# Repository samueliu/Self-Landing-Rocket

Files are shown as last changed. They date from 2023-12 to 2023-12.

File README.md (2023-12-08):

# Self-Landing-Rocket
Democratization of Self-Landing Rocketry Capstone repository

Check out our Youtube Video!
https://m.youtube.com/watch?v=Z3JtFpSVZIc&feature=youtu.be 

# Project Description
The goal of this project is to provide research groups and hobbyists with an open source, sub-scale, self-stabilizing model rocket platform that will unlock previously inaccessible low-budget research/experimentation of 'inverted pendulum' self-landing rockets. This page contains details on the required materials and tools as well as build instructions.

Screenshot 2023-11-28 at 5 56 44 PM

# Fabrication Techniques and Materials
The following machines will be needed for fabrication
1. FDM Printer
2. Resin Printer
3. Desktop CNC Router
4. Soldering Iron
5. Drill
6. Dremel

Additionally, a full list of materials with links to purchasing sites can be found in the materials folder.
# Build/Assembly
There are three main components to this build. The first is machining, printing and cutting parts. The second is soldering the circuit schematic together and the third is epoxying and bolting together the full assembly. 

Step 1: Machining, Printing and Cutting

The parts to print are seperated into resin and FDM parts and can be found under the rocket hardware folder. The majority of the custom components on the vehcile are 3D printed primarily using FDM (Fused Deposition Modeling) but a select few parts were printed on SLA (Stereolithography) 3D printers. The rationale for using the SLA 3D printers primarily revolves around the need for increased component resolution/tolerance. For example, the two pitch and roll servo couplers mate to the T15 servo spline which has 15 teeth size on the order of a single millimeter. For accessability and ease of manufacture, the majority of the remainder of the custom components were printed on a FDM 3D printer as they are generally larger and require less fidelity. A lightweight thermoplastic filament called LW-PLA from PloyMaker was used with low infill (15%) to reduce the wieght of these larger FDM parts. 

A few number of select parts require CNC machining (including the four landing gear legs and the battery holder) as these parts have strict sitffness/mass requirements which could only be satisfied by fiberglass or carbon fiber. In order to meet the stiffness requirements that would be neccesary from supporting the thrust mechanism as well as shock from landing, 3mm Carbon fiber was chosen as the material for the landing gear legs. A desktop CNC router (Shapeoko 4) was used to cut the parts. The feed/punge rate was set to approximately 400mm/s and 150mm/s with a 1/16" 4 flute burr endmill and the CAD/CAM files can be found here under the rocket hardware folder.

A select number of components also required cutting/joining. The two carbon fiber shafts holding the motors were cut using a dremel and the rocket tube was cut using an X-acto knife. A part was also printed to help guide this X acto knife cut and can be found within the STL folder. Super glue was used to couple all 3D printed TVC parts to the respective carbon components except for joints experiencing large loads (carbon legs to rocket fuselage and carbon battery plate to nose cone) which were coupled using an off-the-shelf 5 minute epoxy.

Step 2: Circuit schematic



Above is the circuit schematic used in this project. A proto board was used for integrating all parts. 

Step 3: Putting it all Together

With all materials printed, machined and cut, as well as the electronics put together, the final step is to build the rocket. Provided are both an stl of the full build for easy reference, as well as an instructional manual with step by step build instructions. 

# Assembly details and CAD files

[Instruction Manual](Instruction_Manual.pdf)

[Final CAD Assembly Reference + Files](https://cad.onshape.com/documents/38c71b9123422c3013c80387/w/ad7e7c668ee5186588dc29fc/e/67ed507e38b5f468f95fb797)

[Project Summary & Analysis](Project_Summary_&_Analysis.pdf)

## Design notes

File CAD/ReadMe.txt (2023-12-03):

All of the CAD design for this poject was completed in the OnShape CAD design platform. Access to the OnShape project is by invite only given OnShape restrictions, so please email robbievanzyl@gmail.com to received access.

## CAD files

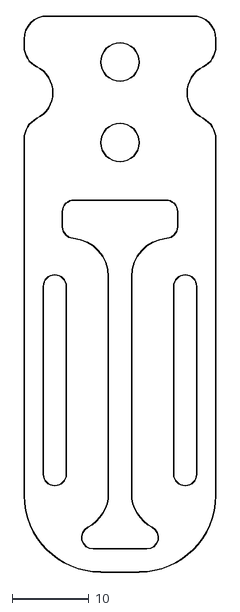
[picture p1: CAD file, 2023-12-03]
CAM/BatteryHolderPlate_CarbonFiber.dxf
25.0 x 72.5

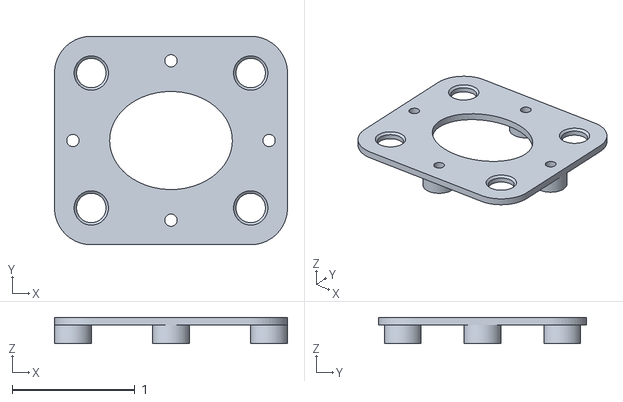
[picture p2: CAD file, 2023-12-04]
STL's/Fuselage and Body/IMU Mount Lower.stl
1.90 x 1.70 x 0.213

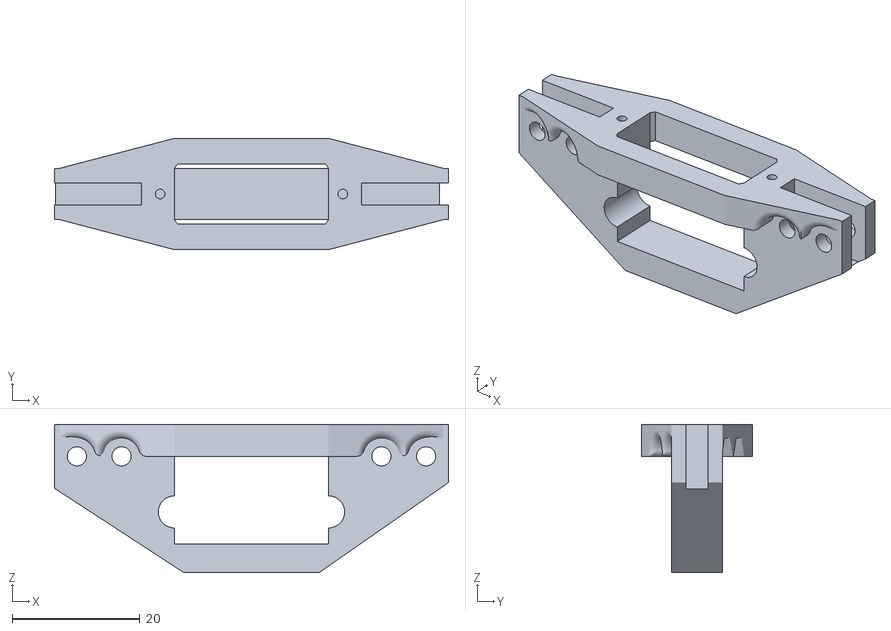
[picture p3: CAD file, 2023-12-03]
STL's/Thrust Vector Control (TVC) Mechanism/ServoLegMount_SLA.stl
61.7 x 17.4 x 23.2

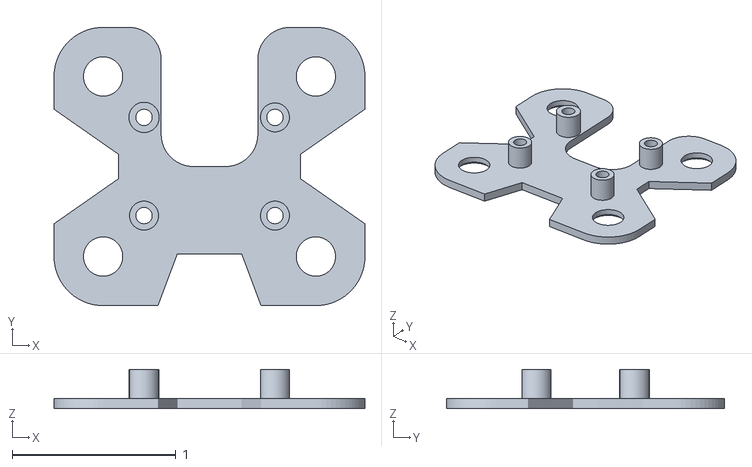
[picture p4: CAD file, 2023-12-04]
STL's/Fuselage and Body/IMU Mount Upper.stl
1.90 x 1.70 x 0.24

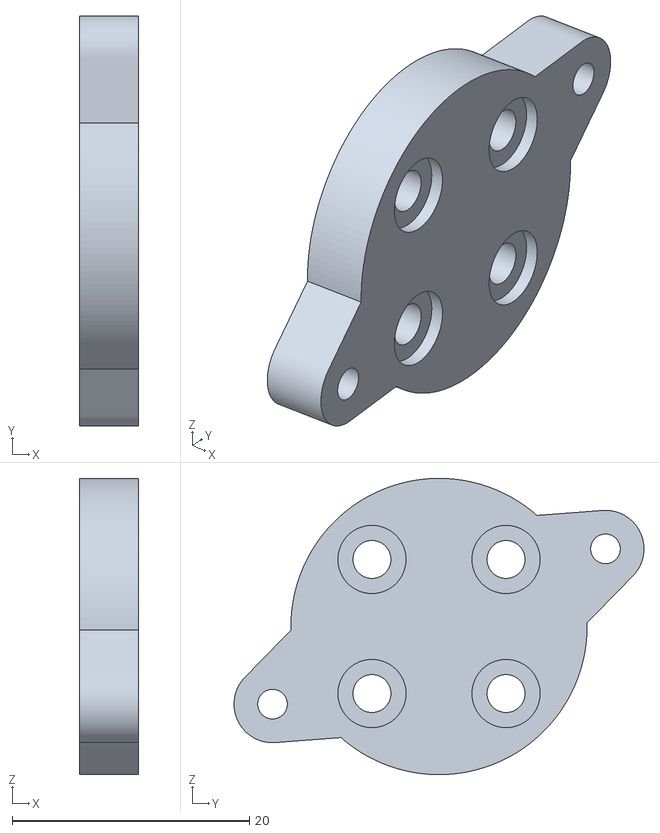
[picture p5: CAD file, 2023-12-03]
STL's/Thrust Vector Control (TVC) Mechanism/TopMotorPlate_SLA.stl
5.00 x 34.6 x 25.0

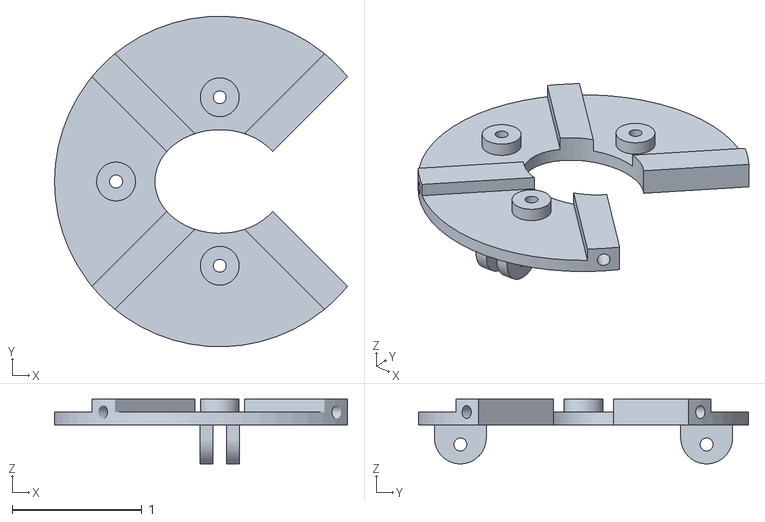
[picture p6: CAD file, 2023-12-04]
STL's/Fuselage and Body/Bottom Sensor Mount Holder.stl
2.26 x 2.55 x 0.5

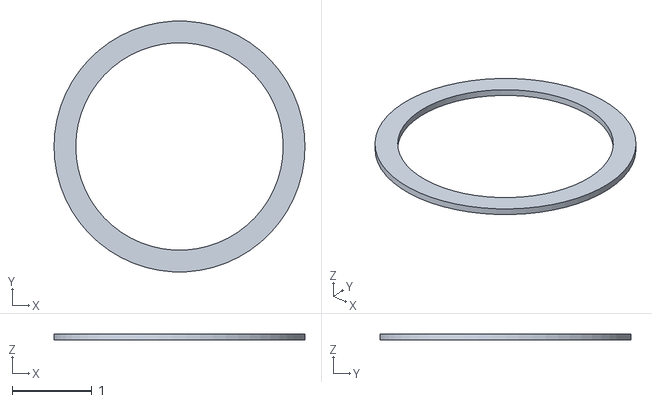
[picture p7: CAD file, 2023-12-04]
STL's/Fuselage and Body/Cutting Guide.stl
3.15 x 3.14 x 0.0787

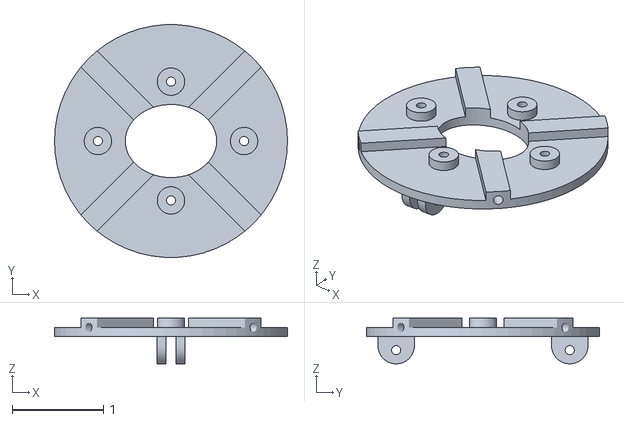
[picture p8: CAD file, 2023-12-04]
STL's/Fuselage and Body/Top Sensor Mount Holder.stl
2.55 x 2.55 x 0.5

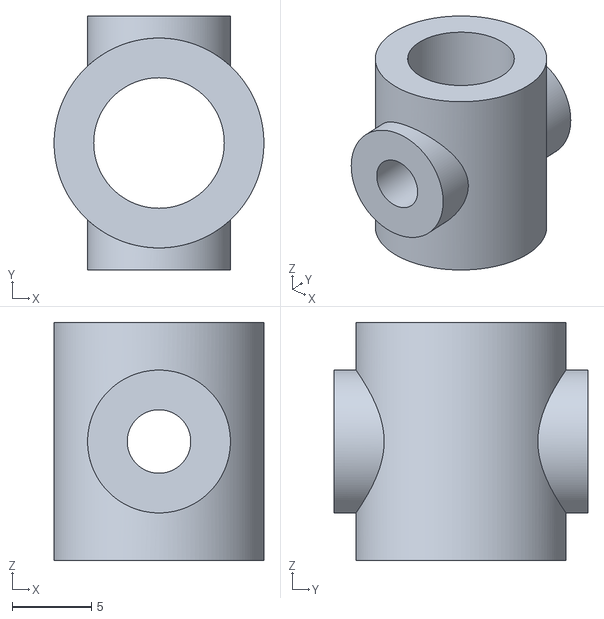
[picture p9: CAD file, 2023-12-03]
STL's/Thrust Vector Control (TVC) Mechanism/CarbonTubePivotPoint_SLA.stl
13.2 x 16.0 x 15.0

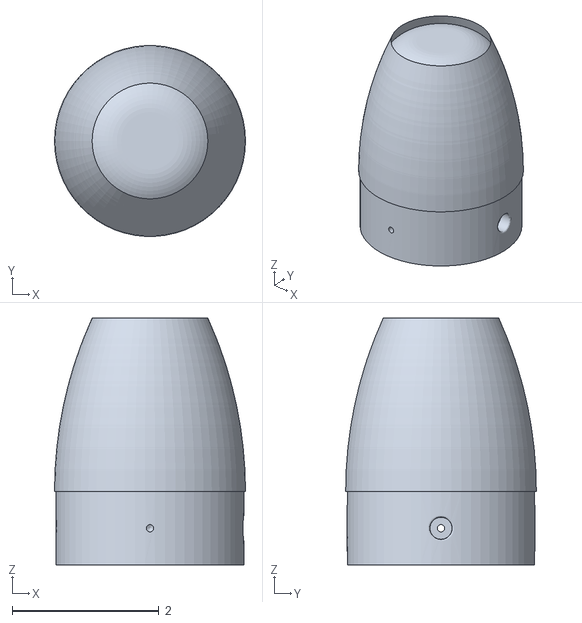
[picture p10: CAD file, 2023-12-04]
STL's/Fuselage and Body/Nose Cone.stl
2.60 x 2.60 x 3.36

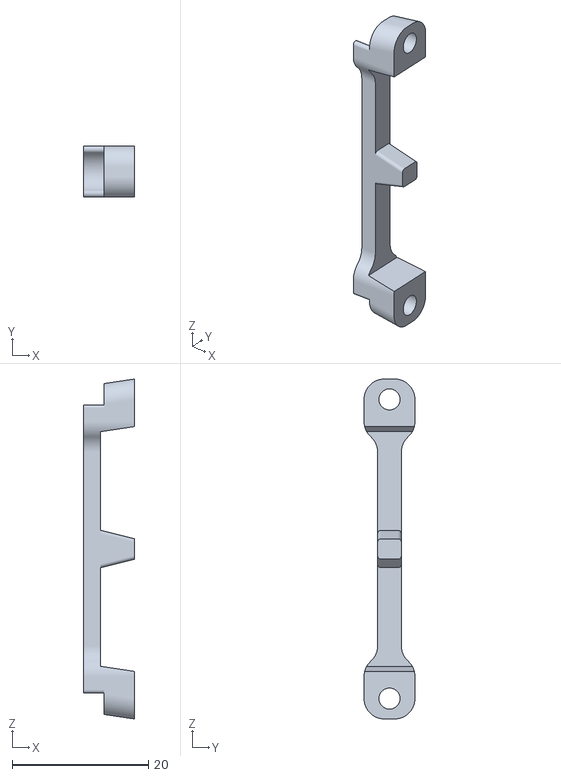
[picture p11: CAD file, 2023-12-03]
STL's/Thrust Vector Control (TVC) Mechanism/ESCHoldingBracket_SLA.stl
7.50 x 7.50 x 50.0

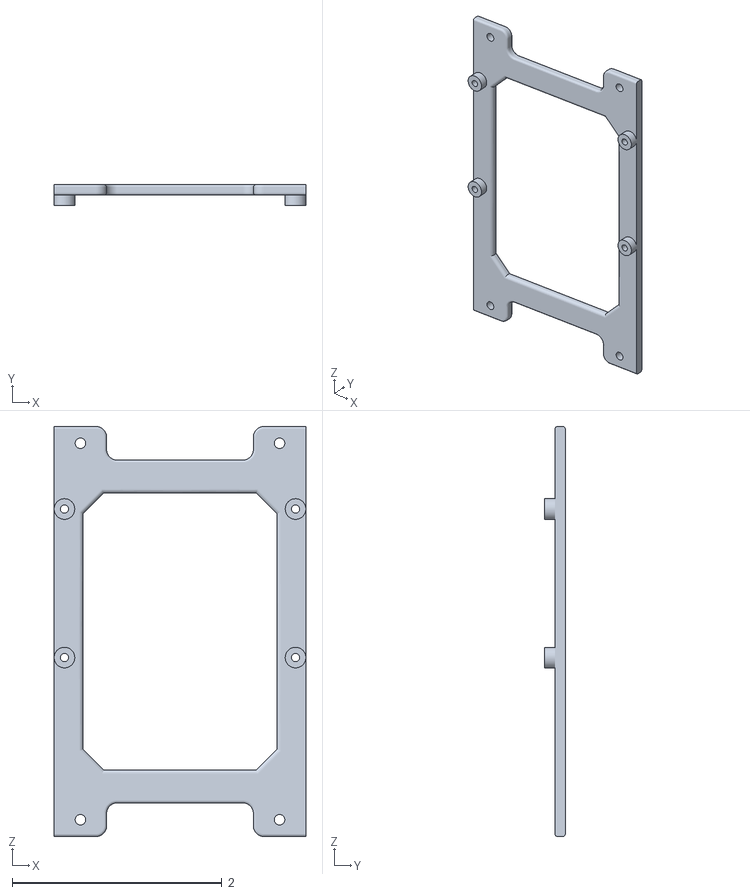
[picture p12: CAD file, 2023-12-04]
STL's/Fuselage and Body/Sensor Mount.stl
2.40 x 0.198 x 3.91

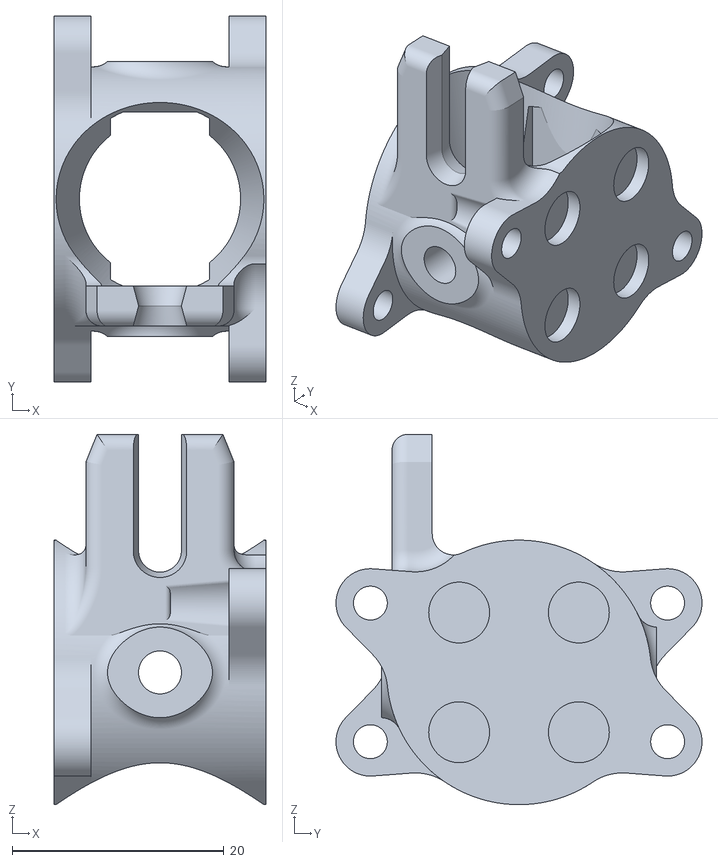
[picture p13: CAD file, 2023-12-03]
STL's/Thrust Vector Control (TVC) Mechanism/MotorPivot_SLA.stl
20.0 x 34.6 x 35.0

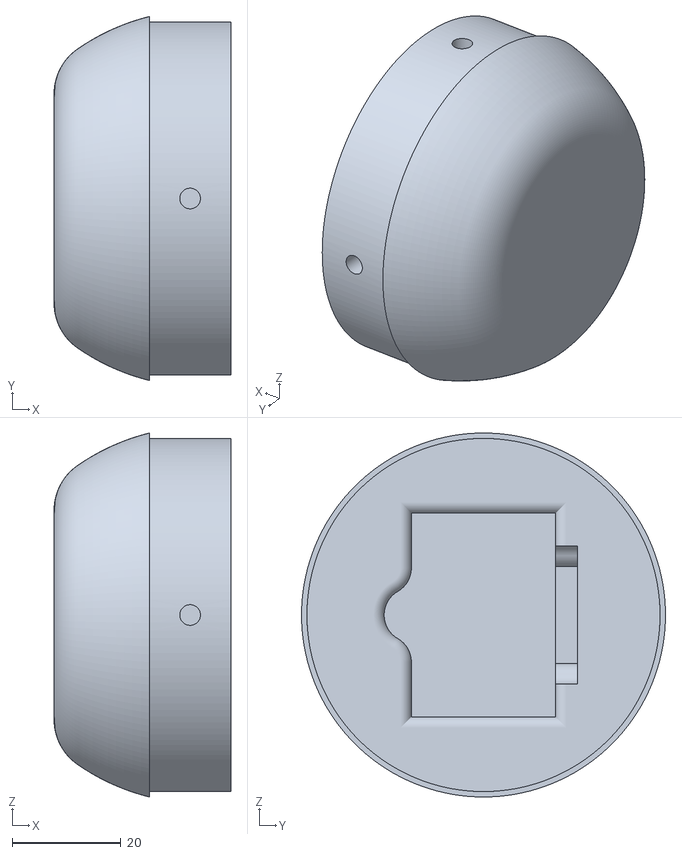
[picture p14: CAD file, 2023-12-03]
STL's/Fuselage and Body/LightweightNoseCone.stl
32.5 x 66.9 x 66.9

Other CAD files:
STL's/Thrust Vector Control (TVC) Mechanism/BottomMotorPlate_SLA.stl
STL's/Thrust Vector Control (TVC) Mechanism/NewMirroredServoLegMount_SLA.stl
STL's/Fuselage and Body/RocketFuselageMount_FDM.stl

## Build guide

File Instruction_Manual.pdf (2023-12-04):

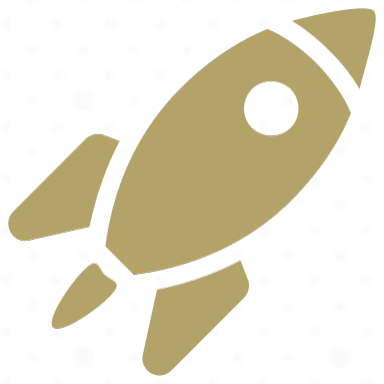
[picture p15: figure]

# Self-Landing Rocket Instructional Manual

# Raise the Ratio!

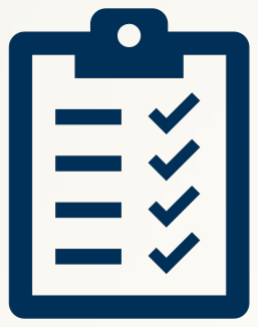
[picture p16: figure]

# Order List

### Electronics Order List

Component Number | Component | Quantity | Vendor | Price
1 | Tattu R-Line 1050mAh 95C 4S1P Lipo Battery Pack (https://genstattu.com/tattu-r-line-1050-mah-4s-1p-95c-lipo-battery-pack-with-xt60-plug.html) | 1 | Tattu | $20.59
2 | Universal Proto-board PCBs 4cm x 6cm (https://www.adafruit.com/product/4785) | 1 | Adafruit | $2.50
3 | Electric Speed Controller (https://www.amazon.com/Electronic-Controller-Brushless-Multicopter-Quadcopter/dp/B09F3G4KNB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) | 2 | Amazon | $39.99
4 | Buck Converter (https://www.amazon.com/ALMOCN-Mini360-Voltage-Converter-4-75V-23V/dp/B08HQDSQZP) | 1 | Amazon | $7.99
5 | Wire spool (https://www.amazon.com/Gauge-Wire-Solid-Hookup-Wires/dp/B088KQFHV7) | 1 | Amazon | $12.99
6 | Corona DS-843MG (https://hobbyking.com/en_us/corona-ds-843mg-digital-high-torque-micro-servo-4-8kg-0-10sec-8-5g.html) | 2 | Hobby King | $12.95
7 | iFlight XING2 2207 4-6S Brushless Motor (https://www.amazon.com/iFlight-Brushless-1855KV-2755KV-Quadcopter/dp/B0B5QVHRV1?th=1) | 2 | Amazon | $32.10
8 | Adafruit 9-DOF Absolute Orientation IMU Fusion Breakout - BNO055 (https://www.adafruit.com/product/4646) | 1 | Adafruit | $29.95
9 | Adafruit BMP390 - Precision Barometric Pressure and Altimeter (https://www.adafruit.com/product/4816) | 1 | Adafruit | $10.95
10 | MicroSD card breakout board+ (https://www.adafruit.com/product/254) | 1 | Adafruit | $7.50
11 | PJRC Teensy 4.0 USB Development
Board (https://www.adafruit.com/product/4323) | 1
Adafruit | $23.80

## ** Example Reference: E2 = Universal Proto-Board

### Hardware Order List

Component Number | Component | Quantity | Vendor | Price
1 | 56 mm X 10" Clear Tube (https://www.apogeerockets.com/Building-Supplies/Body-Tubes/56mm-to-98mm-4in-Tubes/56mm-x-10in-Clear-Tube-BT-70-size-Payload-Tube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) | 1 | Apogee Rockets | $7.56
2 | Propellers (https://www.getfpv.com/gemfan-hurricane-51466-v2-3-blade-propeller-mck-edition-set-of-4.html?vid=14403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) | 2 | GetFPV | $3.99
3 | Carbon Fiber Sheet 300x400x3MM (https://www.amazon.com/dp/B0B8CQVGYD/?coliid=IV4OSQ1LY2OU6&colid=387MZ2VQ52VRI) | 1 | Amazon | $69.99
4 | Large Diameter Carbon Fiber Rod (https://www.mcmaster.com/catalog/129/4116/2153T118) | 1 | McMaster | $24.97
5 | Small Diameter Carbon Fiber Rod (https://www.mcmaster.com/catalog/129/4116/5287T611) | 1 | McMaster | $15.88
6 | Solid Carbon Rod (https://www.mcmaster.com/catalog/129/4116/2153T117) | 1 | McMaster | $17.47
7 | M2 x 10mm | 20 | - -
8 | M3 x 10mm | 26 | - -
9 | M3 x 16mm | 4 | - -
10 | M3 heat set inserts | 8 | - -
11 | Vibration Dampeners (https://www.amazon.com/HONBAY-Vibration-Rubber-Fright-Controller/dp/B073LPTHCL?s=toys-and-games) | 4 | Amazon | $6.59
12 | Zip Ties
15

## ** Example Reference: H2 = Propellers

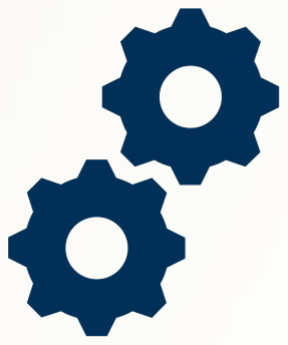
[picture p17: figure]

# Required Equipment

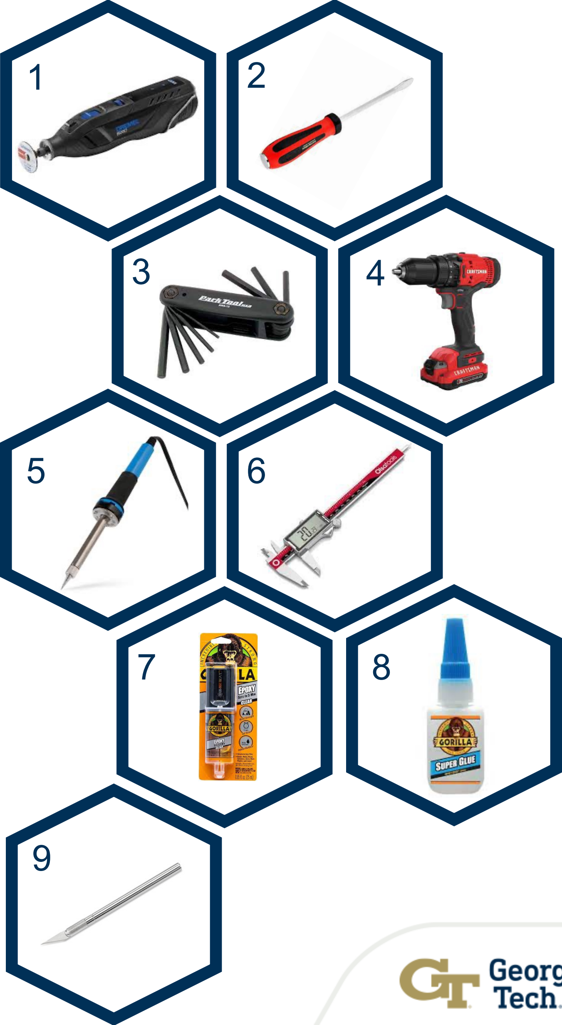
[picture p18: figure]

### Hand Tools

Equipment # | Equipment | Specifications
1 | Dremel | Carbide Dremel Blade
2 | Screwdriver | M1 M2
3 | Allen Key | 2.5 mm 1.5 mm
4 | Drill | 3 mm Drill Bit
5 | Soldering Iron
6 | Calipers / Ruler
7 | Epoxy
8 | Super Glue
9 | Exacto Knife

## ** Example Reference: HT4 = Drill

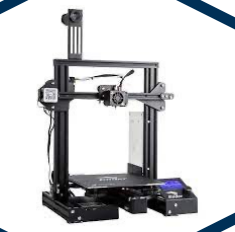
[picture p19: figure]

### Specialty Tools

Equipment # | Equipment | Specifications

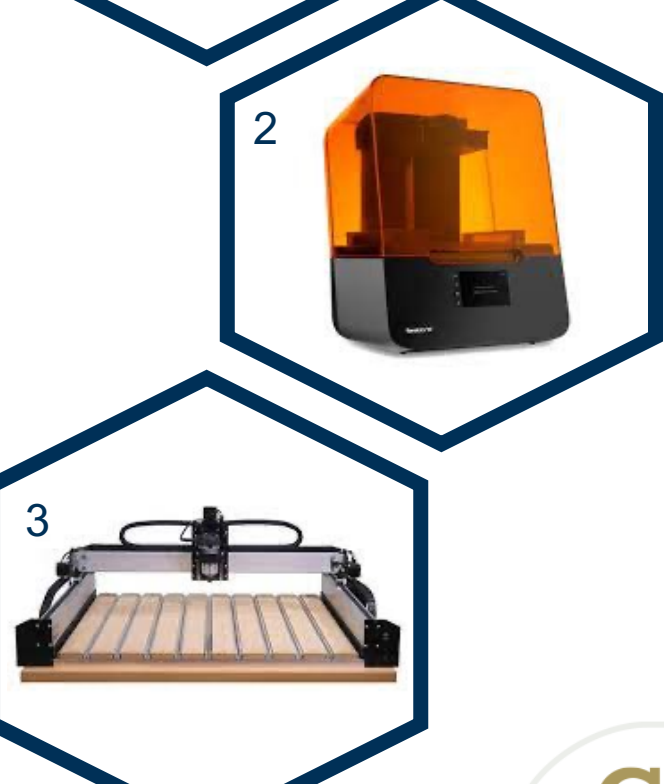
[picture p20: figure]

1 | FDM Printer | Ender 3 was used with .4mm nozzle
2 | Resin Printer | Used Formlabs Form 3, black or clear resin, Adaptive layer height
3 | CNC Router | Shapeoko 4 was used. 400 mm/s feed rate, 150mm/s plunge rate, 1/16" 4 flute burr endmill

1

## ** Example Reference: ST2 = Resin Printer

# 3D Prints

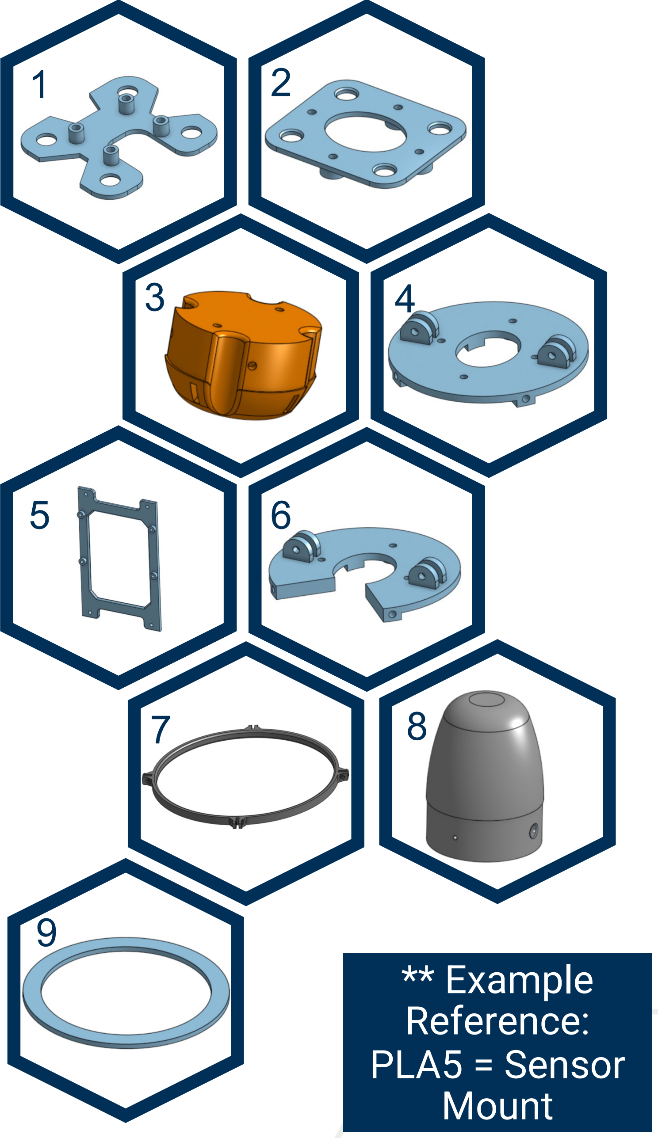
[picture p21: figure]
** Example Reference: PLA5 = Sensor Mount

### Lightweight PLA Printed Parts (Using ST1)

Component # | Component | Quantity | Settings
1 | IMU Mount Upper | 1 | 15% infill, Supports needed on parts 4 and 6, .15mm layer height
2 | IMU Mount Lower | 1
3 | Rocket Fuselage Moun t | 1
4 | Top sensor mount holder | 1
5 | Sensor Mount | 1
6 | Bottom sensor mount holder | 1
7 | Ring Stiffener | 1
8 | Nose Cone | 1
9 | Tube Cutting Guide | 1

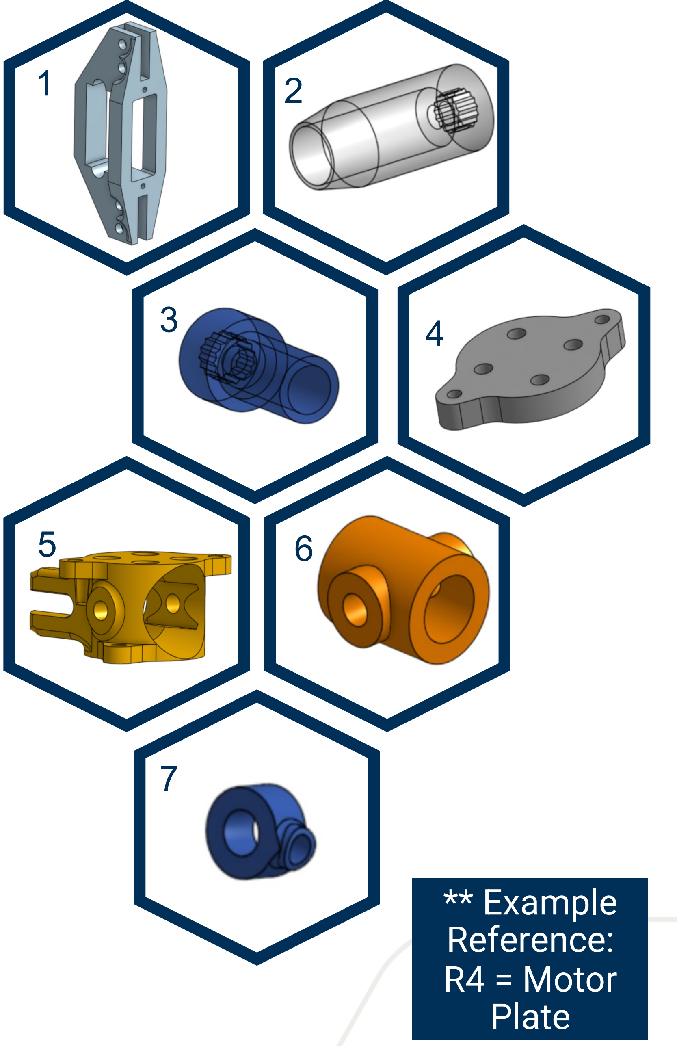
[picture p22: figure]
** Example Reference: R4 = Motor Plate

### Resin Printed Parts (Using ST2)

Component # | Component | Quantity | Settings
1 | Servo Leg Mount | 2 | Printed on Formlabs Form 3, black or clear resin, Adaptive layer height
2 | Smaller Servo Coupler | 1
3 | Larger Servo Coupler | 1
4 | Motor Plate | 2
5 | Motor Pivot | 1
6 | Large diameter carbon tube pivot | 1
7 | Small diameter carbon tube pivot | 1

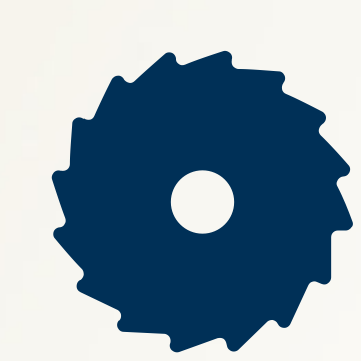
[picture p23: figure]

# CNC Cuts

### CNC Machnied Parts (Using ST3 and H3)

Component # | Component | Quantity | Settings
1 | Large Carbon leg | 2 | Cut on Shapeoko 4. The feed rate was set to approximately 400mm/s and the plunge rate was set to 150mm/s with a 1/16" 4 flute burr endmill
2 | Small Carbon leg | 2
3 | Leg extender | 2

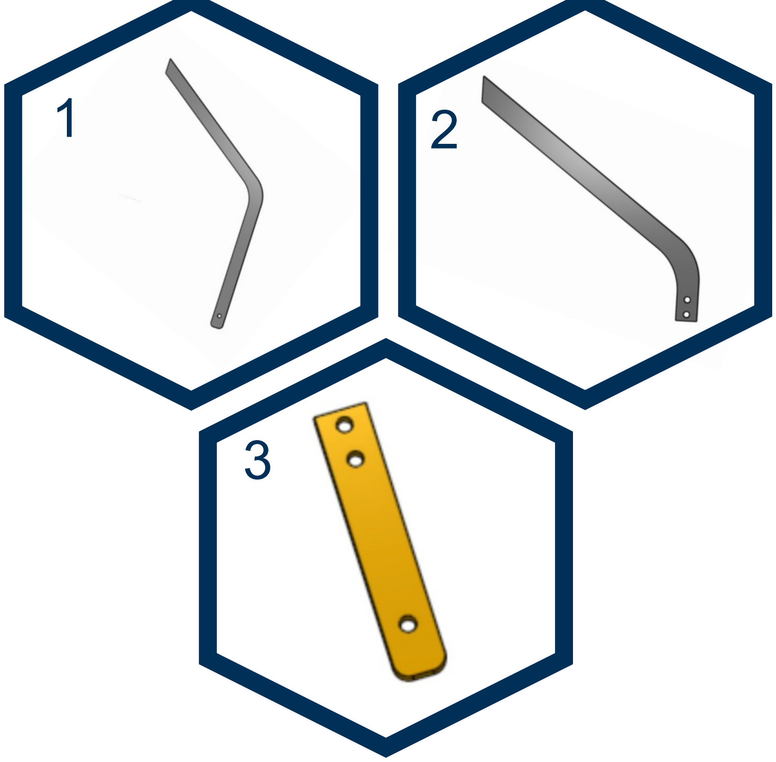
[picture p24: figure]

## ** Example Reference: C1 = Large Carbon leg

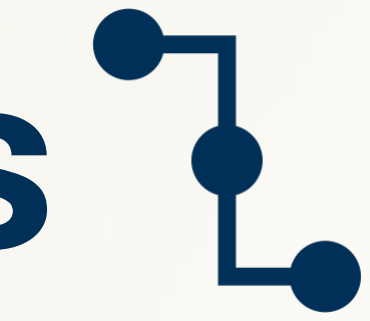
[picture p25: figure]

# Electronics

### Sensor Location Reference

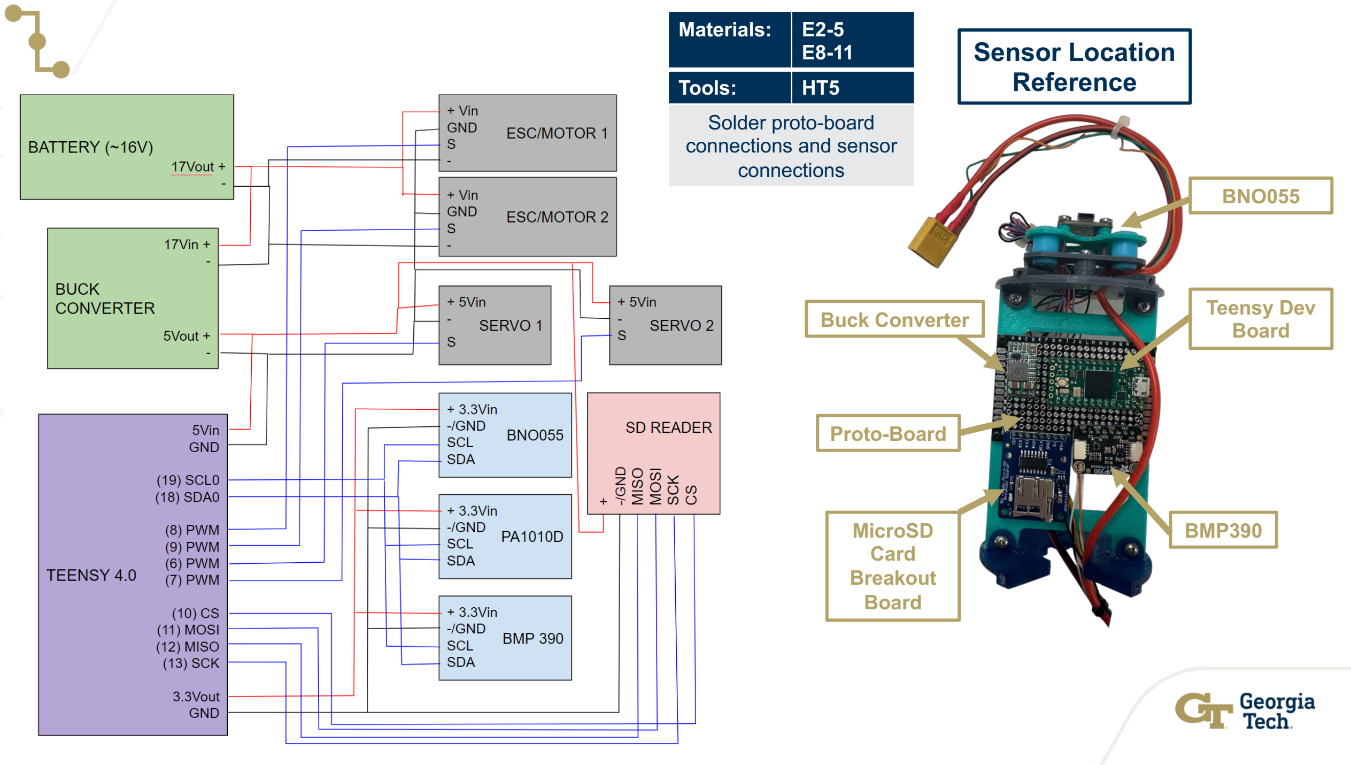
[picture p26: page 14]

Proto-Board

Buck Converter

MicroSD
Card
Breakout
Board

BNO055

Teensy Dev
Board

BMP390

Materials: | E2-5 E8-11
Tools: | HT5
Solder proto-board
connections and sensor
connections

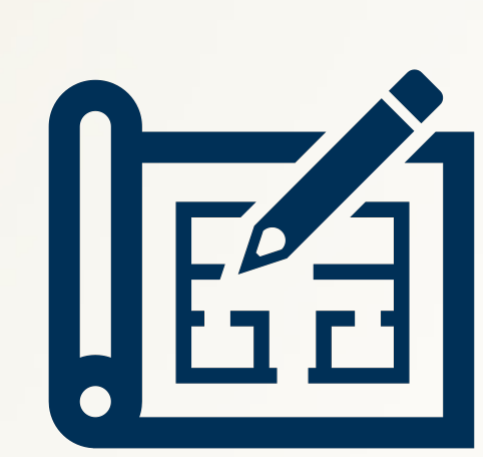
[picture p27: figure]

# Assembly

x2

### Step 1:

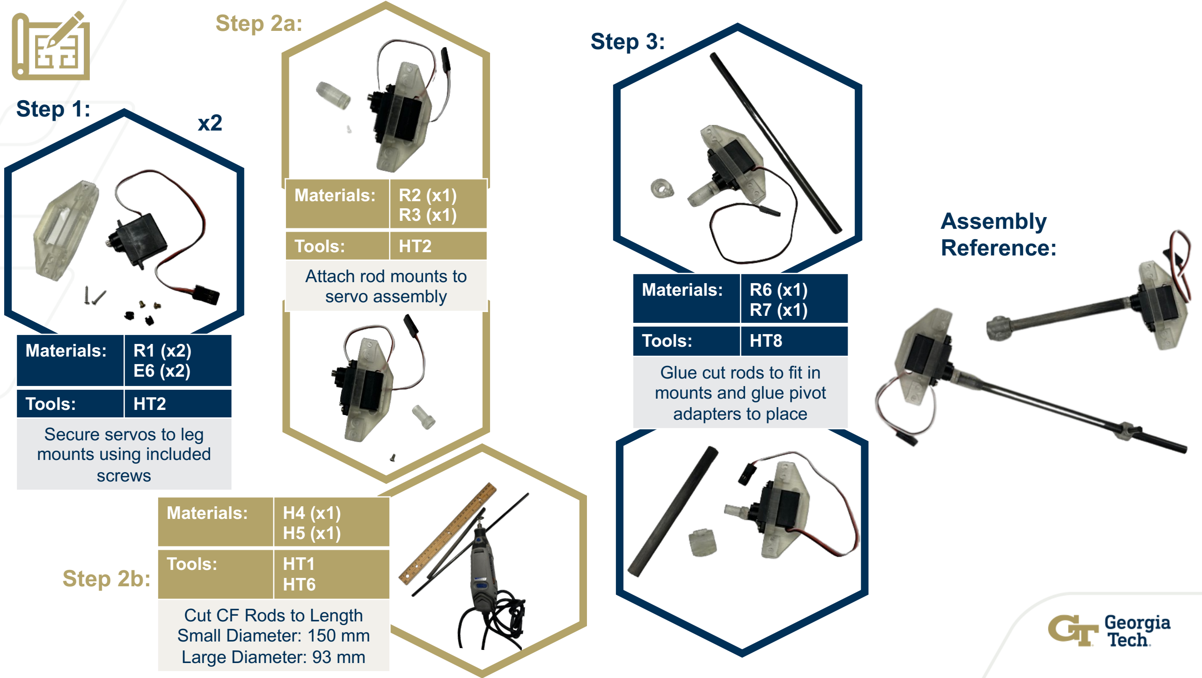
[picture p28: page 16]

Materials: | R2 (x1) R3 (x1)
Tools: | HT2
Attach rod mounts to
servo assembly
Materials: | R1 (x2) E6 (x2)
Tools: | HT2
Secure servos to leg
mounts using included
screws
Materials: | H4 (x1) H5 (x1)
Tools: | HT1 HT6

Cut CF Rods to Length
Small Diameter: 150 mm
Large Diameter: 93 mm

### Step 2a:

### Step 2b:

### Step 3:

Materials: | R6 (x1) R7 (x1)
Tools: | HT8
Glue cut rods to fit in
mounts and glue pivot
adapters to place

### Assembly Reference:

### x2 Step 4:

Step 5a: | Step 6:

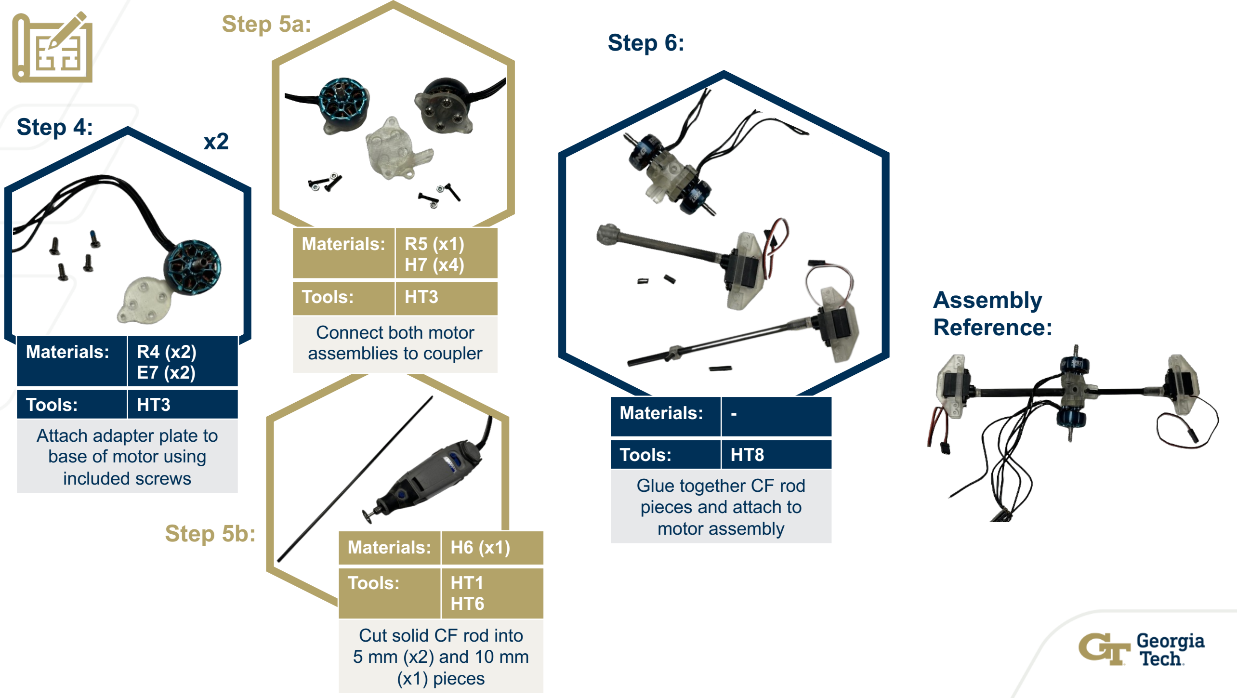
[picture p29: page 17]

### Assembly Reference:

Step 5b: | Materials: | H6 (x1)
| Tools: | HT1 HT6

Cut solid CF rod into
5 mm (x2) and 10 mm
(x1) pieces
Materials: | R4 (x2) E7 (x2)
Tools: | HT3
Attach adapter plate to
base of motor using
included screws
Materials: | -
Tools: | HT8
Glue together CF rod
pieces and attach to
motor assembly
Materials: | R5 (x1) H7 (x4)
Tools: | HT3

Connect both motor
assemblies to coupler

### Step 7:

### Step 8:

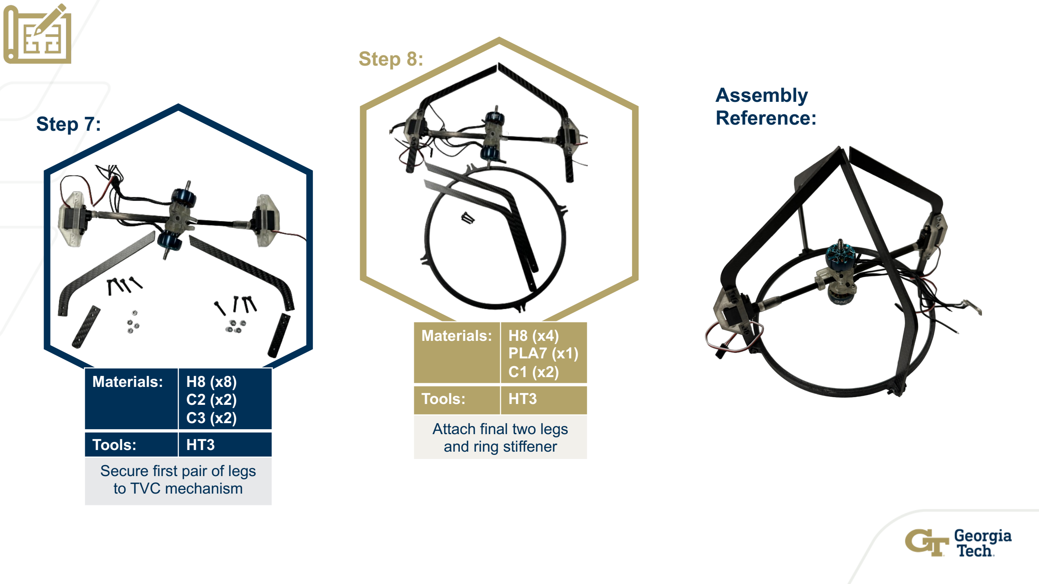
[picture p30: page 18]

### Assembly Reference:

Materials: | H8 (x4) PLA7 (x1) C1 (x2)
Tools: | HT3

Attach final two legs
and ring stiffener
Materials: | H8 (x8) C2 (x2) C3 (x2)
Tools: | HT3
Secure first pair of legs
to TVC mechanism

### Step 10:

### Step 9a:

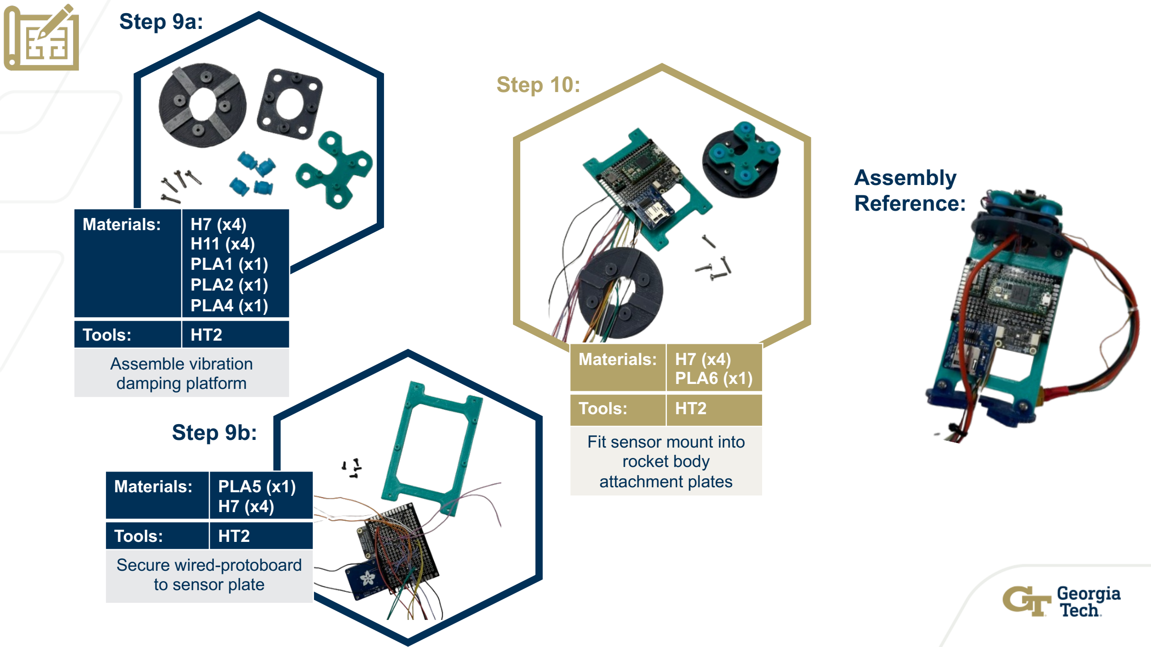
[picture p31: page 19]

### Assembly Reference:

### Step 9b:

Materials: | H7 (x4) PLA6 (x1)
Tools: | HT2

Fit sensor mount into
rocket body
attachment plates
Materials: | H7 (x4) H11 (x4) PLA1 (x1) PLA2 (x1) PLA4 (x1)
Tools: | HT2
Assemble vibration
damping platform
Materials: | PLA5 (x1) H7 (x4)
Tools: | HT2
Secure wired-protoboard
to sensor plate

### Step 11:

### Step 12a:

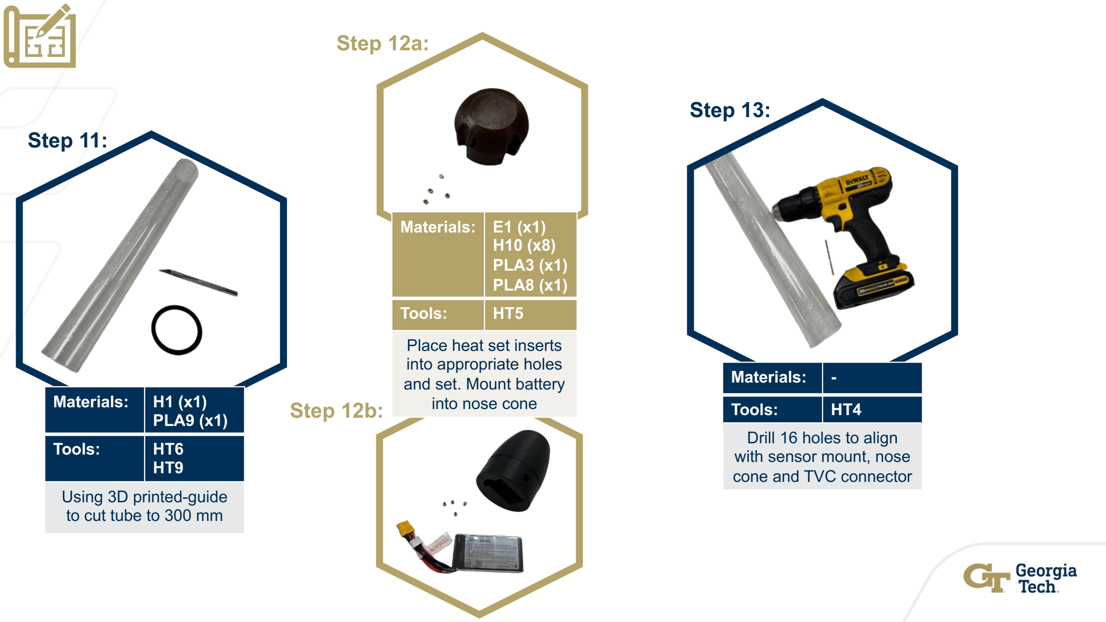
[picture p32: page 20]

Materials: | H1 (x1) PLA9 (x1)
Tools: | HT6 HT9

Using 3D printed-guide
to cut tube to 300 mm

### Step 12b:

Materials: | E1 (x1) H10 (x8) PLA3 (x1) PLA8 (x1)
Tools: | HT5

Place heat set inserts
into appropriate holes
and set. Mount battery
into nose cone

### Step 13:

Materials: | -
Tools: | HT4
Drill 16 holes to align
with sensor mount, nose
cone and TVC connector

### Final Assembly

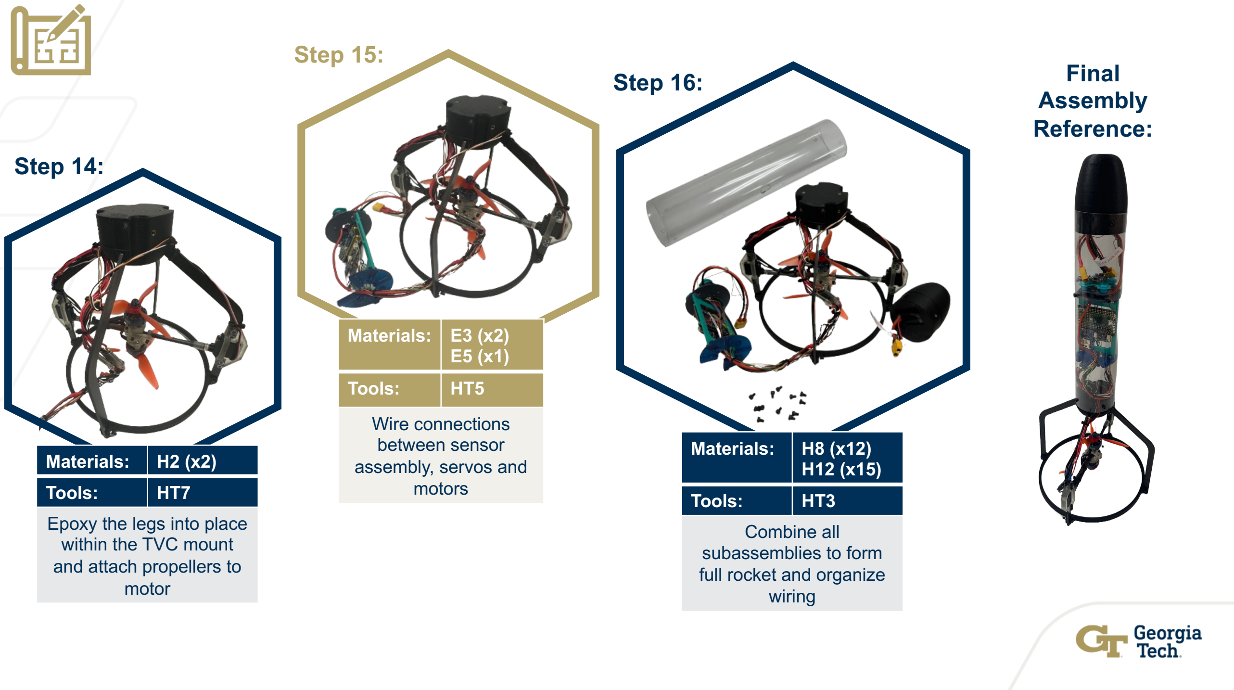
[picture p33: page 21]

Materials: | H2 (x2)
Tools: | HT7
Epoxy the legs into place
within the TVC mount
and attach propellers to
motor
Materials: | E3 (x2) E5 (x1)
Tools: | HT5

Wire connections
between sensor
assembly, servos and
motors
Materials: | H8 (x12) H12 (x15)
Tools: | HT3
Combine all
subassemblies to form
full rocket and organize
wiring

### Reference: Step 14:

### Step 15: Step 16:

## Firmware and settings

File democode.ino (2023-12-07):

// The following code is a very basic skeleton code that initializes all sensors and allows simple data reading.

#include <Wire.h>
#include <Adafruit_Sensor.h>
#include <Adafruit_BMP3XX.h>
#include <Adafruit_BNO055.h>
#include <Adafruit_GPS.h>
#include <Servo.h>
#include <SD.h>

#define BMP_I2C_ADDRESS 0x77 // or 76?
#define BNO_I2C_ADDRESS 0x29 // or 28?
#define GPS_I2C_ADDRESS 0x10

// Customize here pulse lengths as needed
#define MIN_PULSE_LENGTH 1000 // Minimum pulse length in µs
#define MID_PULSE_LENGTH 1100 // Mid pulse length in µs
#define MAX_PULSE_LENGTH 1200 // Maximum pulse length in µs

// Initialize motor objects
Servo motA;
Servo motB;

// Initialize TVC servo objects
Servo servoA;
Servo servoB;

// Initialize sensor objects
Adafruit_BMP3XX bmp;
Adafruit_BNO055 bno(BNO_I2C_ADDRESS);
Adafruit_GPS gps(&Wire);

char data;      // variable for motor data
int pos = 0;    // variable to store the servo position 

// Pin numbers for Teensy 4.0 according to wiring schematic!
const int CS_SD = 10;
const int MOSI_SD = 11;
const int MISO_SD = 12;
const int SCK_SD = 13;
const int SCL0 = 19;
const int SDA0 = 18;

int i = 0;


void setup() {
  // put your setup code here, to run once:
  Serial.begin(9600);
  Serial.println("Starting");

  // Initialize the pressure sensor
  if (!bmp.begin_I2C(BMP_I2C_ADDRESS)) {
    Serial.println("Check BMP!");
    while (1);
  }

  // Initialize IMU
  if (!bno.begin()) {
    Serial.println("Check BNO!");
    while (1);
  }

  // Initialize the GPS
  gps.begin(GPS_I2C_ADDRESS);

  servoA.attach(6);  // attaches the servo on pin 6
  servoB.attach(7); // attaches the servo on pin 7

  // //For now DO NOT RUN motor portion with propellers on! Motors fire at max speed during calibration sometimes
  // motA.attach(8, MIN_PULSE_LENGTH, MAX_PULSE_LENGTH); //motor on pin 8
  // motB.attach(9, MIN_PULSE_LENGTH, MAX_PULSE_LENGTH); //motor on pin 9
}

void loop() {
  // put your main code here, to run repeatedly:

  // Read data from BMP390
  bmp.performReading();
  Serial.print("Pressure: ");
  Serial.print(bmp.pressure);
  Serial.println(" Pa");

  // Read data from BNO055
  sensors_event_t event;
  bno.getEvent(&event);
  Serial.print("Orientation: ");
  Serial.print(event.orientation.x);
  Serial.print(", ");
  Serial.print(event.orientation.y);
  Serial.print(", ");
  Serial.println(event.orientation.z);

  // Read data from PA1010D
  char c = gps.read();
  Serial.write(c);

  // Twitch pitch servo of TVC
  servoA.write(90);
  delay(1000);
  servoA.write(105);
  delay(1000);
  servoA.write(90);
  delay(1000);
  servoA.write(75);
  delay(1000);
  servoA.write(90);
  delay(1000);

  // Twitch yaw servo of TVC
  servoB.write(90);
  delay(1000);
  servoB.write(105);
  delay(1000);
  servoB.write(90);
  delay(1000);
  servoB.write(75);
  delay(1000);
  servoB.write(90);

  //Code to fire up motors (DO NOT RUN! Motors currently have bug that runs at 100% speed at calibration!)
  // motA.writeMicroseconds(MIN_PULSE_LENGTH);
  // motB.writeMicroseconds(MIN_PULSE_LENGTH);
  // motA.writeMicroseconds(MAX_PULSE_LENGTH);
  // motB.writeMicroseconds(MAX_PULSE_LENGTH);
  // delay(4000);
  // motA.writeMicroseconds(MIN_PULSE_LENGTH);
  // motB.writeMicroseconds(MIN_PULSE_LENGTH);

  delay(45000);
}
